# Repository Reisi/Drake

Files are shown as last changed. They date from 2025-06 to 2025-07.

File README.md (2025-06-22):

# Drake

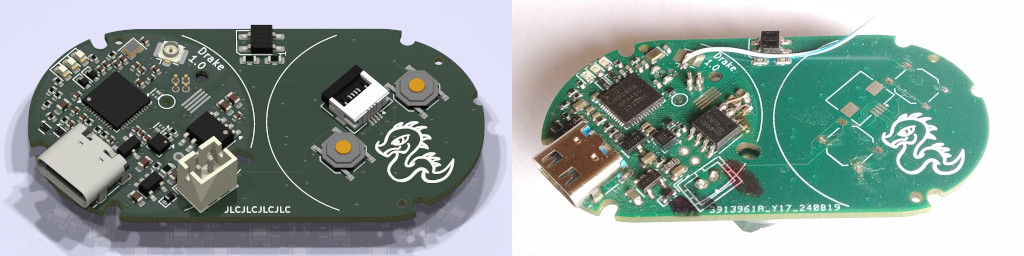
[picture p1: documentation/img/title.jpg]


The Drake hardware is a multi-purpose PCB which can be used to build a wireless dropper post actuator or a rear light.

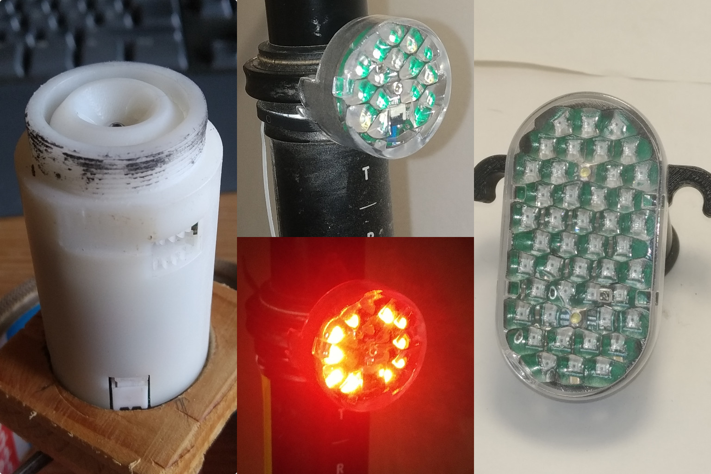
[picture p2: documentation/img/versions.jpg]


## Actuator

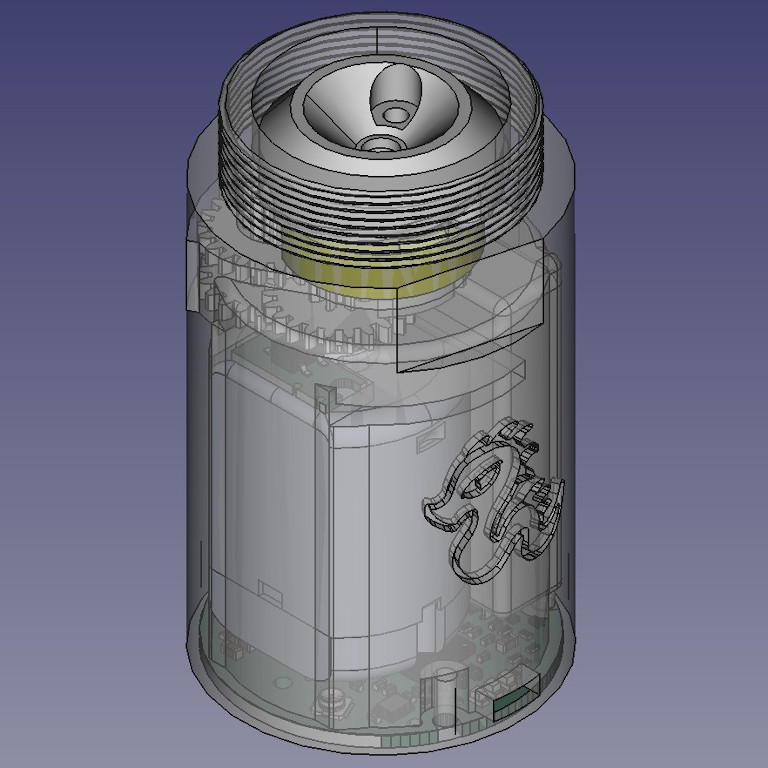
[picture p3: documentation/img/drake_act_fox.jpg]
Actuator


### Features

- Bluetooth connectivity for remote control and configuration.
- I2C connectivity for control, configuration and sensor readings.
- construction files for Fox Transfer dropper posts available

## Light

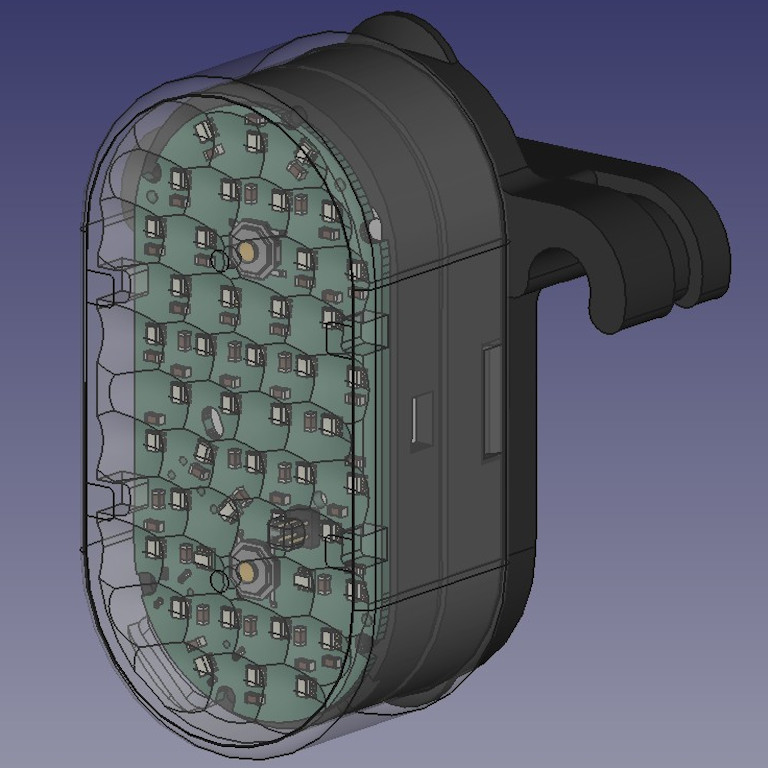
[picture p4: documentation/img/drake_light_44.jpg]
Light_44
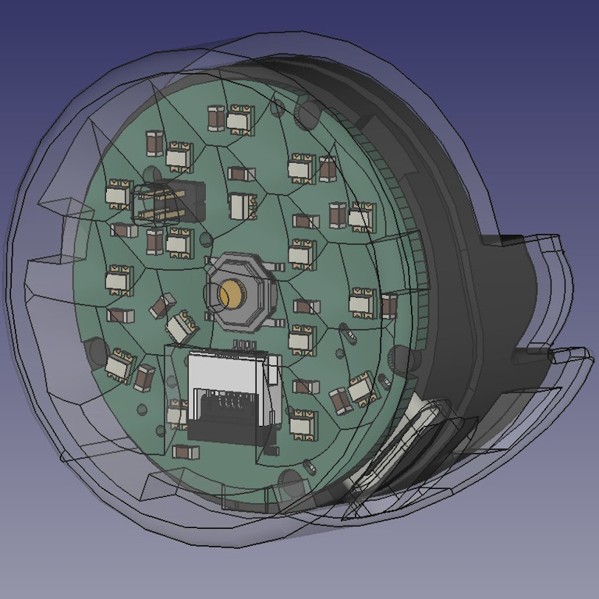
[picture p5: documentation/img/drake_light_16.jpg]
Light_16
 

### Features

- two configurations with either 16 or 44 WS2812 LEDs
- 8 configurable modes
- configurable LED pattern
- ability to control a dropper actuator over a FFC (using I2C)

## Firmware

Drake is part of The Helen Project. The source code and compiled firmware files are available [here](https://github.com/Reisi/The_Helen_Project/tree/master/Firmware/Helen/boards/Drake_10)

## License

This project is licensed under the BSD-2-clause License - see the [license.txt](license.txt) file for details

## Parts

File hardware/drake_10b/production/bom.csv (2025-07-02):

Designator | Footprint | Quantity | Value | LCSC Part #
AE2 | U.FL_Hirose_U.FL-R-SMT-1_Vertical | 1 | GT-RF1125A-01G | C5299419
C1, C2, C69, C70 | 0402 | 4 | 12p | C1547
C10, C12, C13, C15, C18 | 0603 | 5 | 10u | C19702
C14, C16, C20, C4, C66, C68, C8, C9 | 0402 | 8 | 100n | C307331
C17, C19, C7 | 0402 | 3 | 1u | C52923
C21, C22, C23, C24, C25, C26, C27, C28, C29, C30, C31, C32, C33, C34, C35, C36, C37, C38, C39, C40, C41, C42, C43, C44, C45, C46, C47, C48, C49, C50, C51, C52, C53, C54, C55, C56, C57, C58, C59, C60, C61, C62, C63, C64, C65, C67 | 0603 | 46 | 100n | C14663
C3 | 0402 | 1 | 0p8 | C1550
C6 | 0402 | 1 | 100p | C1546
D1, D15, D2 | D_SOD-523 | 3 | H5VND5UB | C20615819
D10, D11, D12, D13, D14, D17, D18, D19, D20, D22, D23, D24, D25, D26, D27, D28, D29, D30, D31, D32, D33, D34, D35, D36, D37, D38, D39, D40, D41, D42, D43, D44, D45, D46, D47, D48, D49, D50, D51, D52, D53, D55, D7, D8, D9 | LED_WS2812B-2020_PLCC4_2.0x2.0mm | 45 | WS2812B-2020 | C2976072
D16, D21, D3, D54 | Diodes_DFN1006-3 | 4 | H5VU13U | C20615795
D4 | 0603 | 1 | red | C2286
D5 | 0603 | 1 | yellow | C89811
D6 | 0603 | 1 | white | C2290
J2 | USB_C_Receptacle_XKB_U262-16XN-4BVC11 | 1 | USB_C_Receptacle_USB2.0_16P | C2931474
J3 | JST_PH_B2B-PH-K_1x02_P2.00mm_Vertical | 1 | Li-Ion | C131337
J5, J6, J8 | Jushuo_AFC01-S04FCC-00_1x04-1MP_P0.50_Horizontal | 3 | Conn_01x04 | C262260
JP1 | 0402 | 1 | Jumper_2_Bridged | C17168
L1 | 0402 | 1 | 3n9 | C14033
R1, R2 | 0402 | 2 | 22 | C25092
R10, R3, R8 | 0402 | 3 | 1M | C26083
R11, R12, R15, R16, R4 | 0402 | 5 | 3k3 | C25890
R13 | 0402 | 1 | 75k | C25798
R14, R17, R18 | 0402 | 3 | 1k5 | C25867
R5, R7, R9 | 0402 | 3 | 5k1 | C25905
R6 | 0603 | 1 | 2r2 | C22939
SW1, SW2, SW3, SW4 | SW_Push_1P1T_XKB_TS-1187A | 4 | SW_Push | C318884
U1 | QFN-48-1EP_6x6mm_P0.4mm_EP4.6x4.6mm | 1 | nRF52832-QFxx | C77540
U2 | SOT-23-3 | 1 | XC6206P332MR-G | C5446
U3 | SOT-23-5 | 1 | TP4054 | C32574
U4 | LGA-12_2x2mm_P0.5mm | 1 | LIS2DH12TR | C110926
U5 | SOIC-8_3.9x4.9mm_P1.27mm | 1 | BDR6125
U6 | Everlight_ITR1201SR10AR | 1 | ITR8307-S18-TR8 | C409524
Y1 | Crystal_SMD_2016-4Pin_2.0x1.6mm | 1 | Crystal_GND24 | C2965584

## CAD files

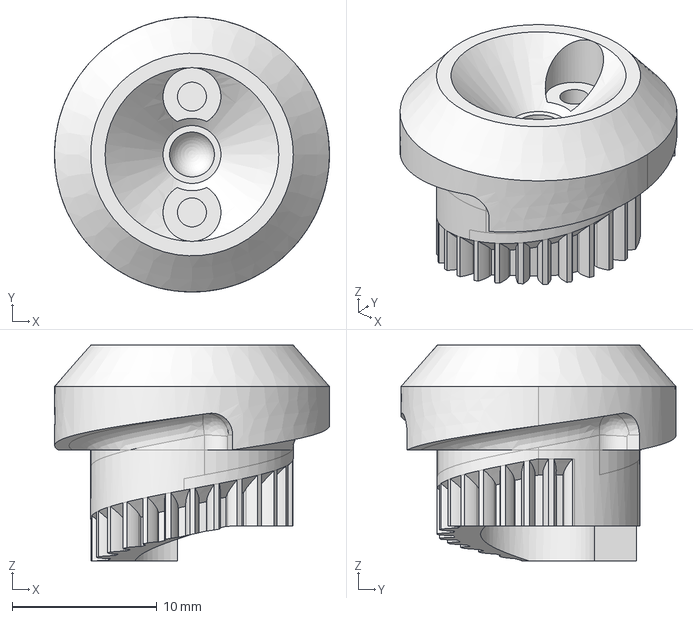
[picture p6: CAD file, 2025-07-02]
construction/Drake_Fox/Drake_Fox_2208_v2b-plunger.step
19.0 x 19.0 x 14.9 mm

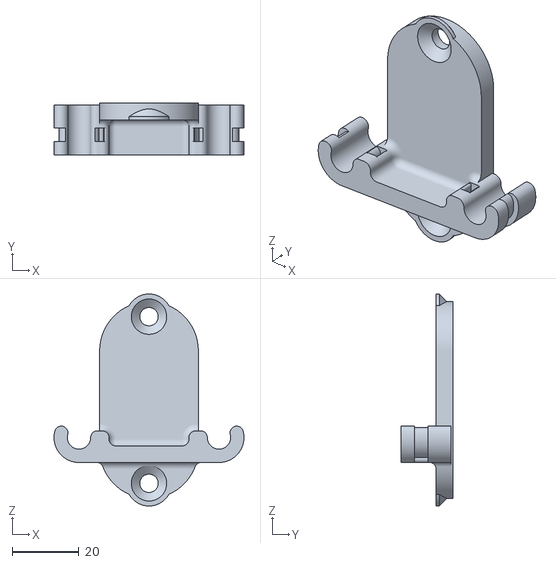
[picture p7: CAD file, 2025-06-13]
construction/Drakelight/Drakelight_MountVertical.stl
57.0 x 15.5 x 63.6

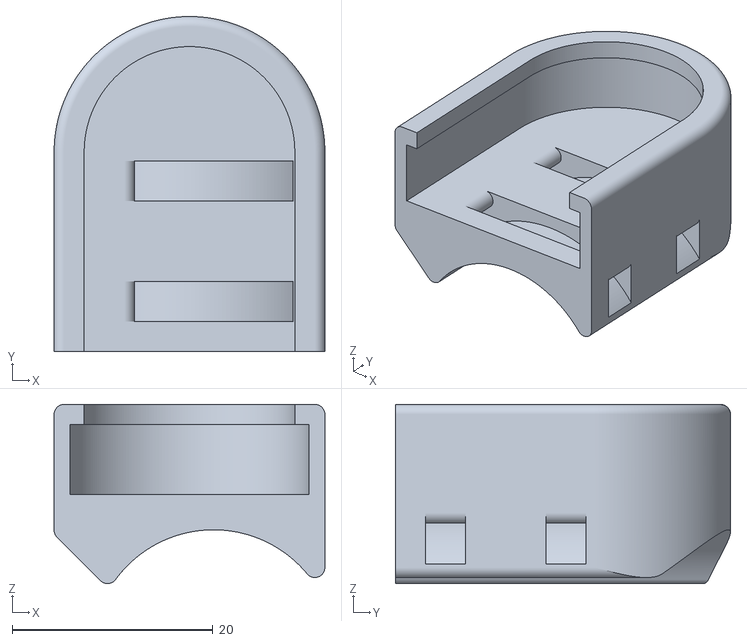
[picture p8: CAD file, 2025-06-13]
construction/Remote_Mount/XiaomiYiMount_hor.stl
27.0 x 33.4 x 17.9

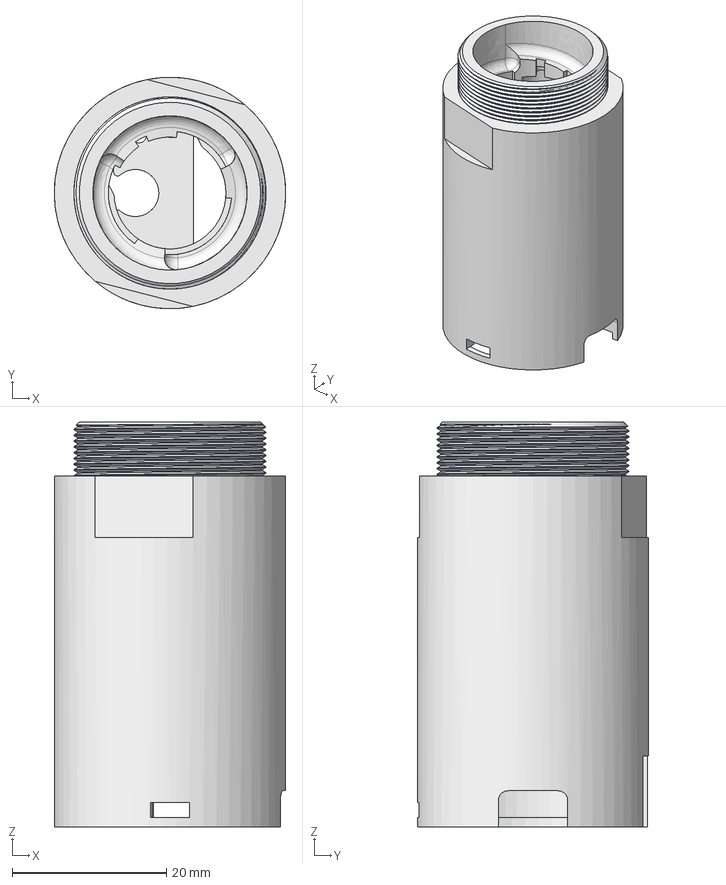
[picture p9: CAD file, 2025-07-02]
construction/Drake_Fox/Drake_Fox_2208_v2b-case.step
30.0 x 30.0 x 52.5 mm

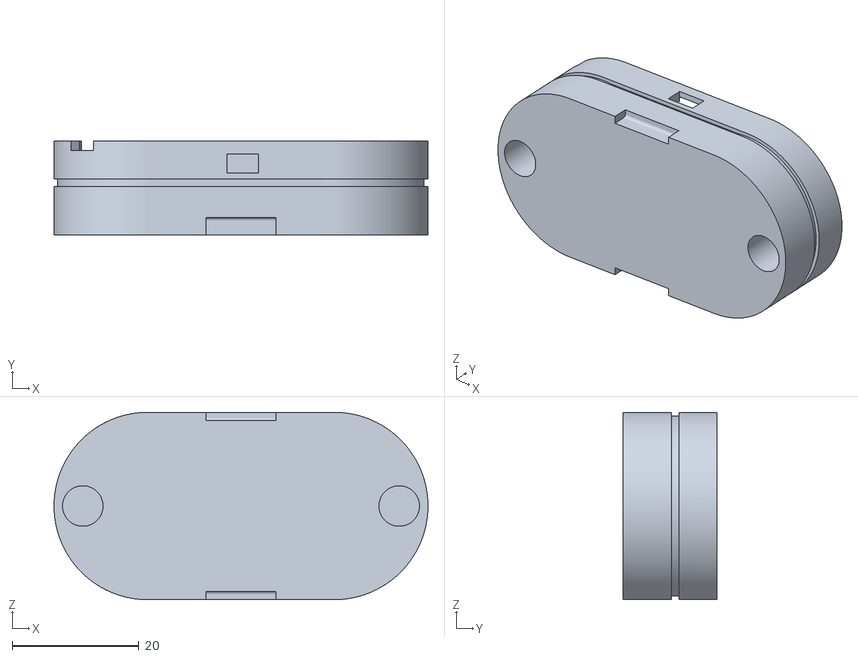
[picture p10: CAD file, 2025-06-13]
construction/Drakelight/Drakelight_case.stl
59.1 x 14.8 x 29.6

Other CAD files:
construction/Remote_Mount/XiaomiYiMount.FCStd
construction/Drake_Fox/Drake_Fox_2208_v2b-plunger.stl

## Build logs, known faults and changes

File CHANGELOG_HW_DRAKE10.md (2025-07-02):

# Changelog
All notable changes to the Drake board hardware will be documented in this file.

The format is based on [Keep a Changelog](https://keepachangelog.com/en/1.0.0/)

## [1.1] - 2025-07
### Added

### Changed
- changed acceleration sensor to MMA8451Q
- changed motor driver to DRV8213

### Removed

### Fixed

### Known Issues

## [1.0b] - 2025-06
### Changed
- changed green LED to yellow and blue LED to white

### Fixed
- fixed swapped power supply pins for motor driver
- changed R13 value to 82k

## [1.0] - 2024-08
### Known Issues
- VCC and GND pin swapped on moter driver
- R13 changed from 1k5 to 82k (ir receiver resitor)

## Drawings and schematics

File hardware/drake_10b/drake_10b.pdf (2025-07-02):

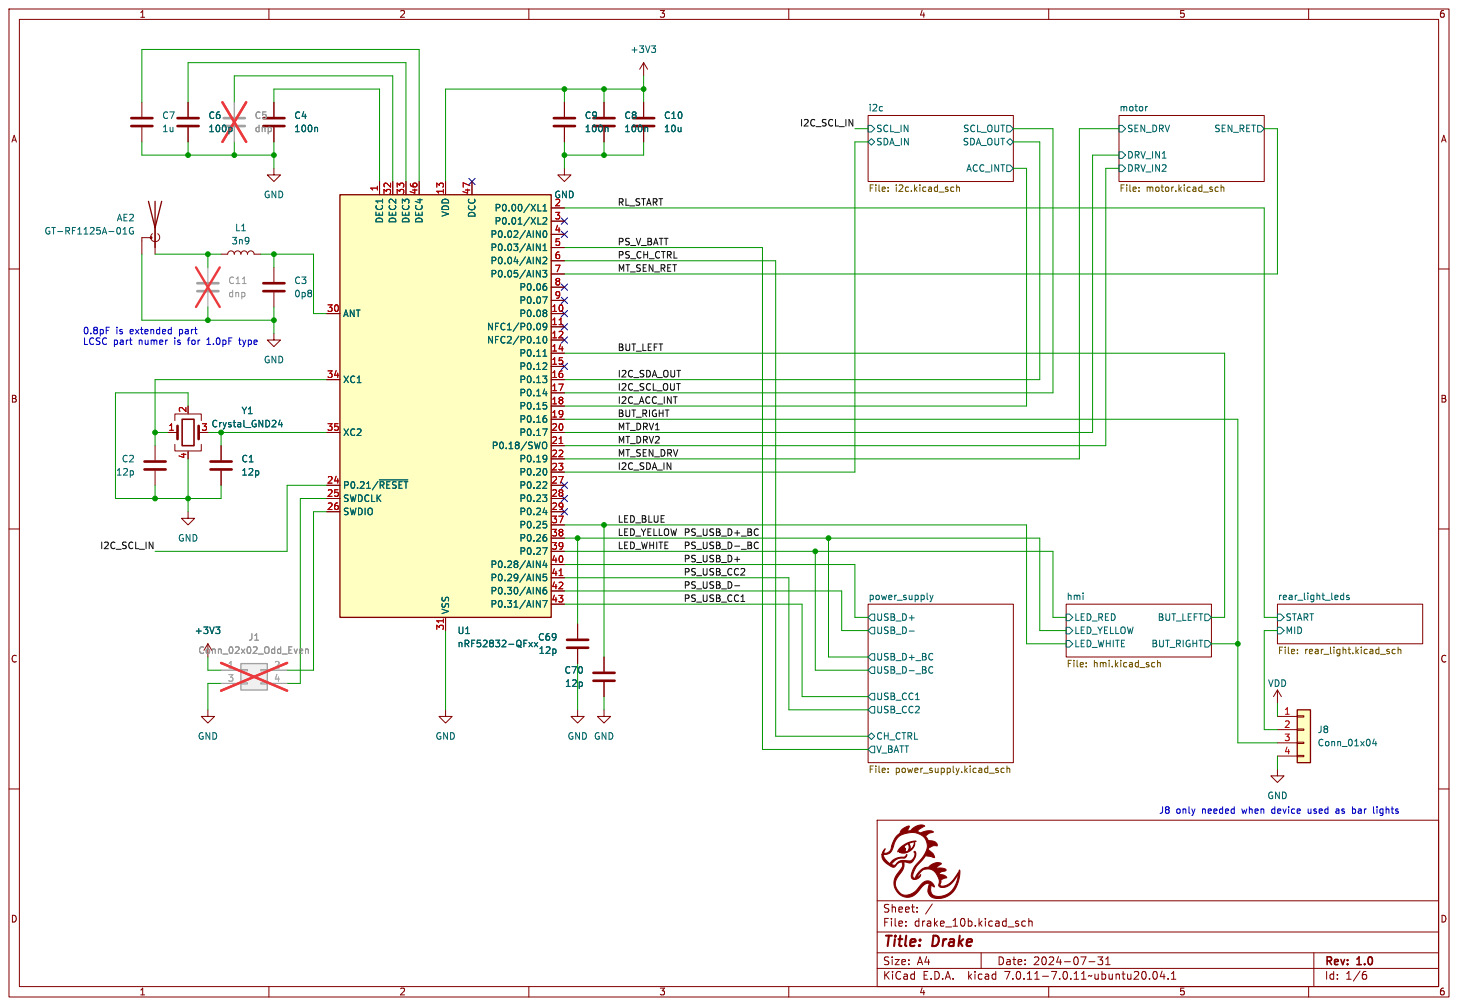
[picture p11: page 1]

1 P0.08 10 NFC1/P0.09 11 NFC2/P0.10 12 VDD 13 P0.11 14 P0.12 15 P0.13 16 P0.14 17 P0.15 18 P0.16 19 P0.00/XL1 2 P0.17 20 P0.18/SWO 21 P0.19 22 P0.20 23 P0.21/~{RESET} 24 SWDCLK 25 SWDIO 26 P0.22 27 P0.23 28 P0.24 29 P0.01/XL2 3 ANT 30 VSS 31 DEC2 32 DEC3 33 XC1 34 XC2 35 P0.25 37 P0.26 38 P0.27 39 P0.02/AIN0 4 P0.28/AIN4 40 P0.29/AIN5 41 P0.30/AIN6 42 P0.31/AIN7 43 DEC4 46 DCC 47 P0.03/AIN1 5 P0.04/AIN2 6 P0.05/AIN3 7 P0.06 8 P0.07 9 U1

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

J8 only needed when device used as bar lights

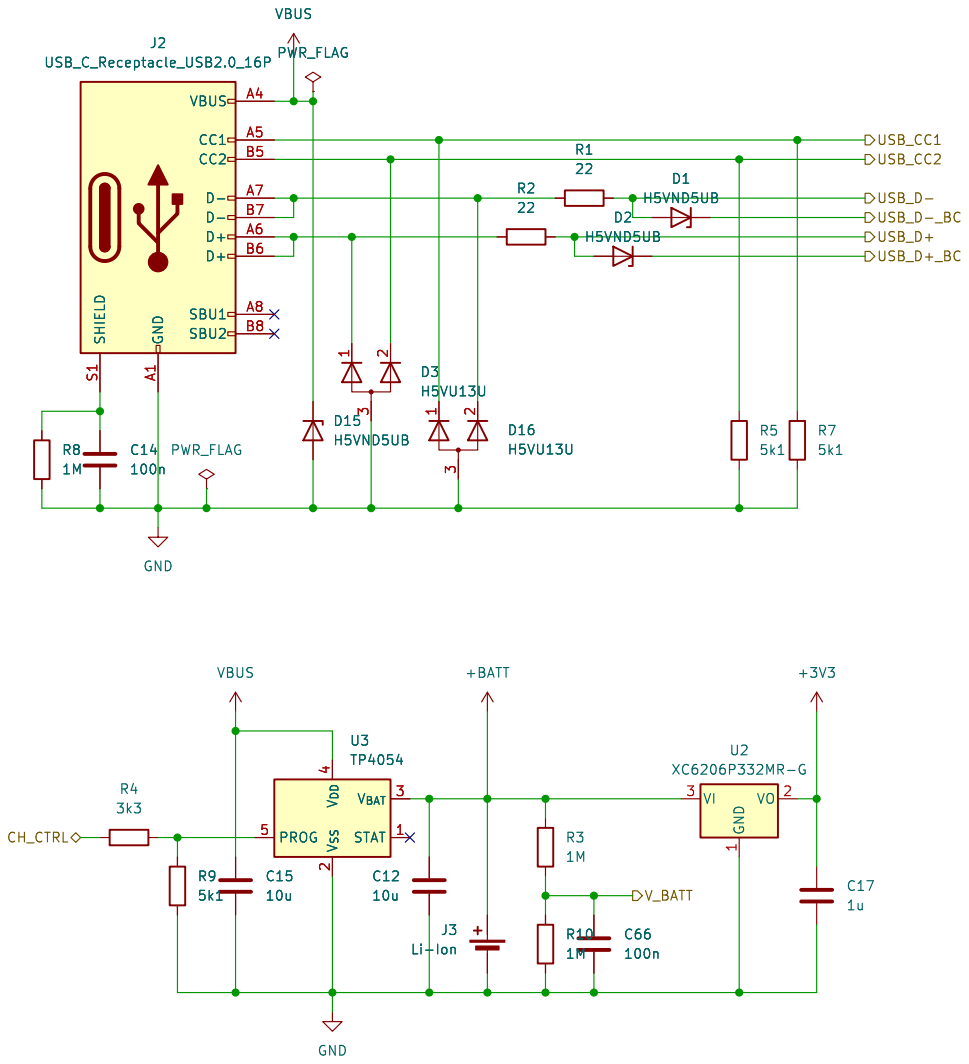
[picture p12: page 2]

File: power_supply.kicad_sch Sheet: /power_supply/
Id: 2/6 Title: power supply

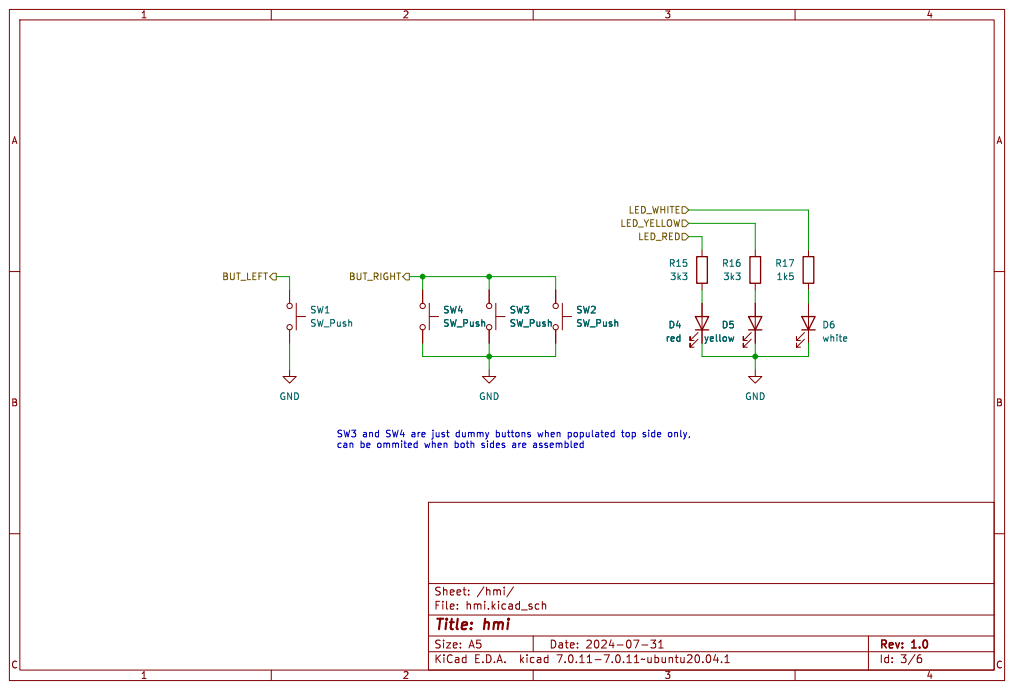
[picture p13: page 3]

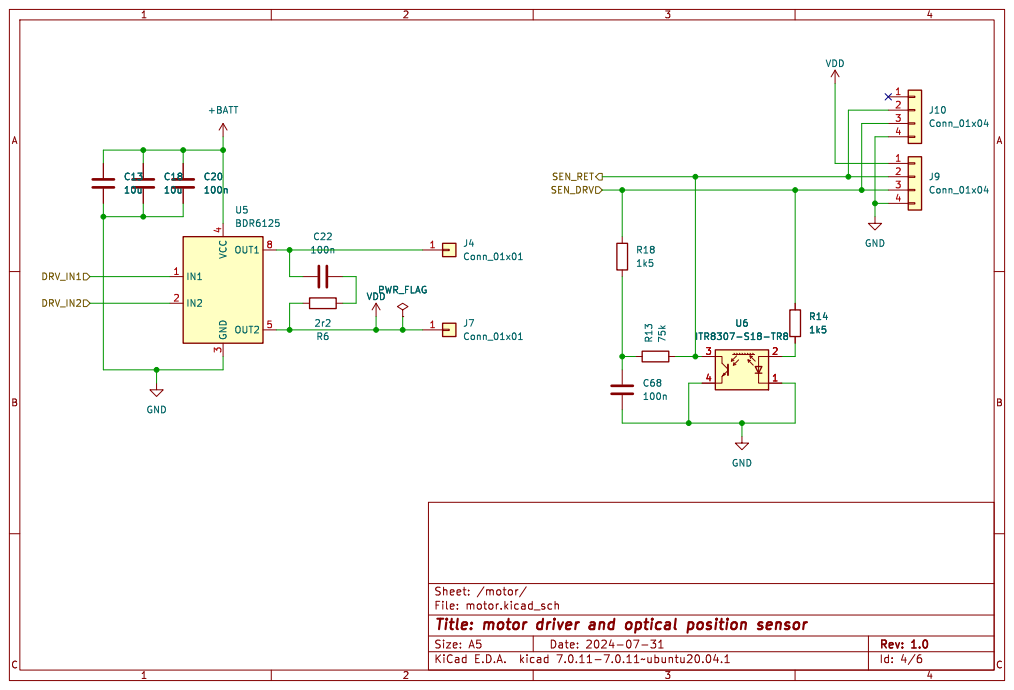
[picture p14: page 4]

Id: 4/6 Title: motor driver and optical position sensor File: motor.kicad_sch Sheet: /motor/ R6

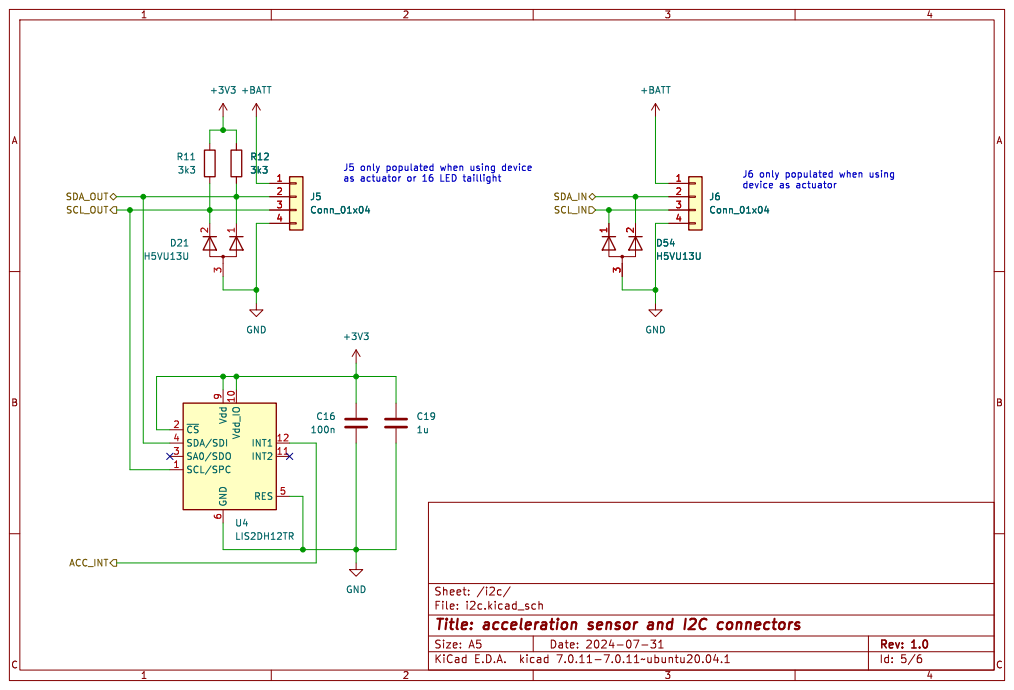
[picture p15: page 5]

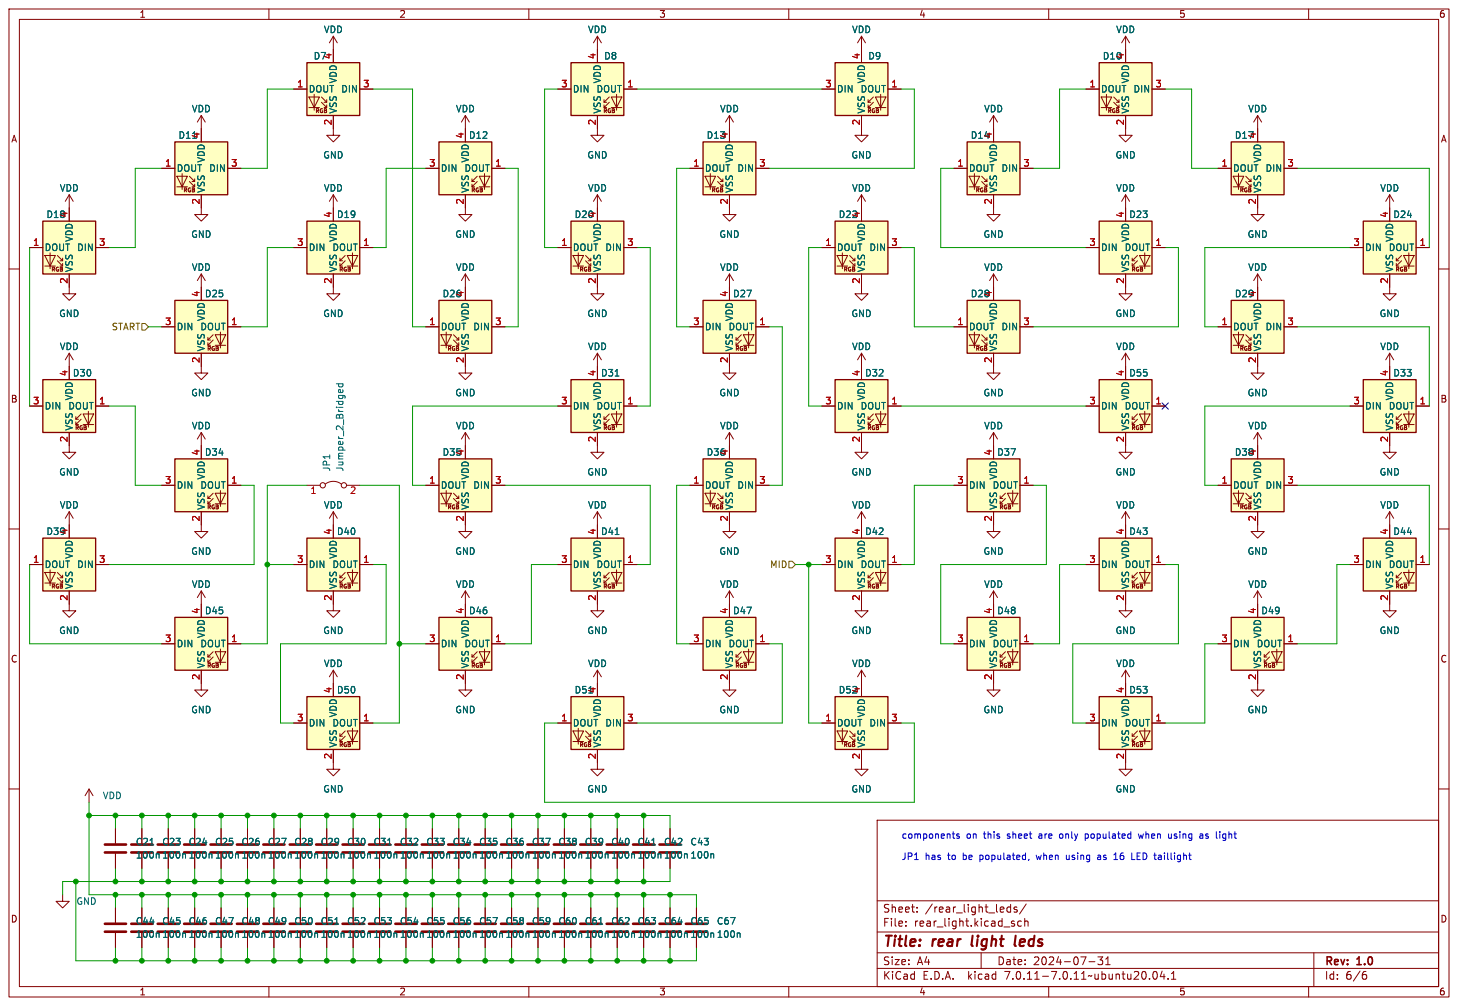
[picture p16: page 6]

4D53 VDD GND GND GND

Id: 6/6 Title: rear light leds

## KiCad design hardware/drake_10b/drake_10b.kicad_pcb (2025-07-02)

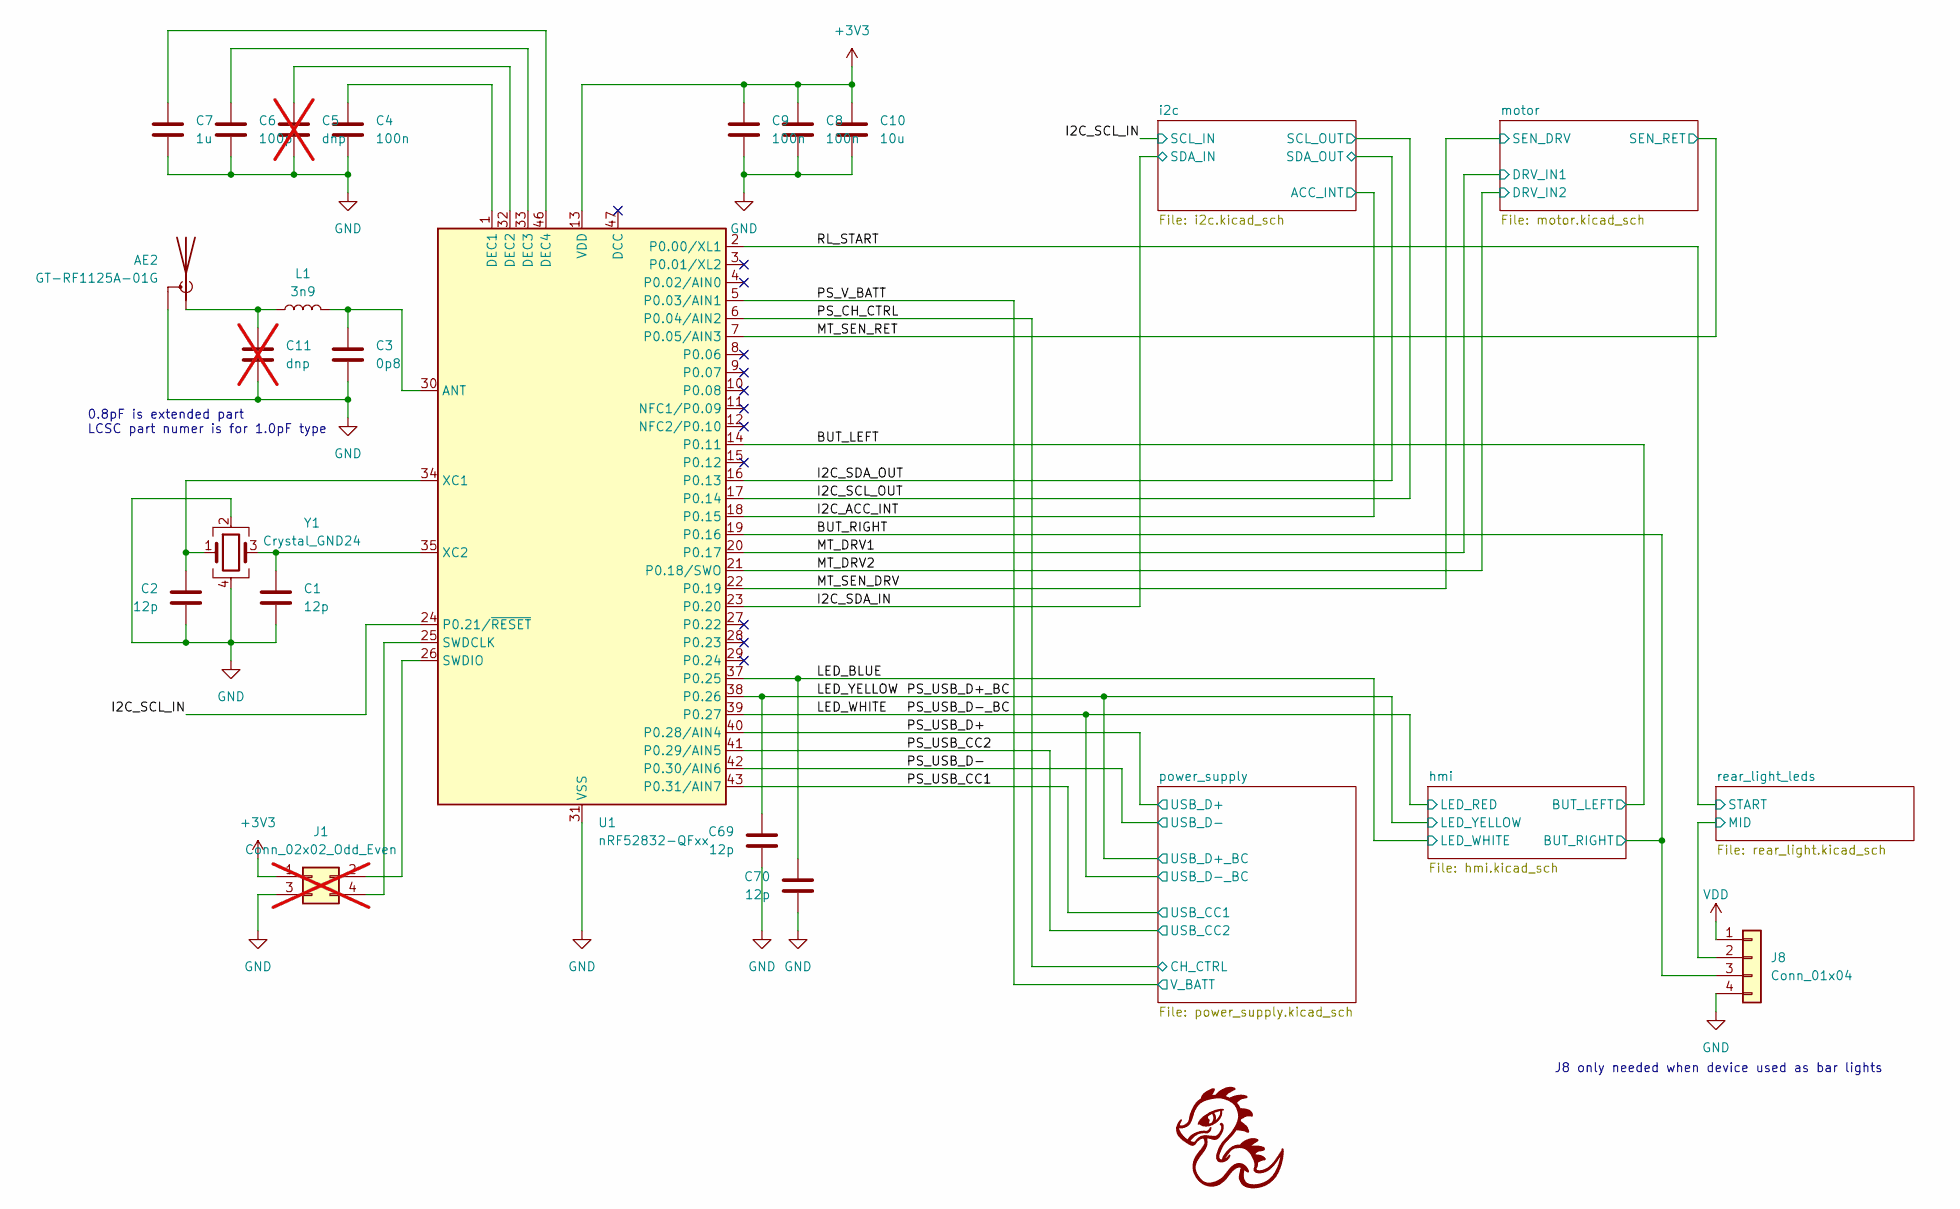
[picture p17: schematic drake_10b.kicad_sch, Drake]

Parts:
AE2: GT-RF1125A-01G; U.FL_Hirose_U.FL-R-SMT-1_Vertical; JLC SMD
C1, C2, C69, C70: 12p; C_0402_1005Metric; JLC 0402
C3: 0p8; C_0402_1005Metric; JLC 0402
C4, C8, C9: 100n; C_0402_1005Metric; JLC 0402
C5, C11: dnp; C_0402_1005Metric; not fitted
C6: 100p; C_0402_1005Metric; JLC 0402
C7: 1u; C_0402_1005Metric; JLC 0402
C10: 10u; C_0603_1608Metric; JLC 0603
J1: Conn_02x02_Odd_Even; PinHeader_2x02_P1.27mm_Vertical; not fitted
J8: Conn_01x04; Jushuo_AFC01-S04FCC-00_1x04-1MP_P0.50_Horizontal; JLC SMD,P=0.5mm
L1: 3n9; L_0402_1005Metric; JLC 0402
U1: nRF52832-QFxx; QFN-48-1EP_6x6mm_P0.4mm_EP4.6x4.6mm; JLC QFN-48-EP(6x6)
Y1: Crystal_GND24; Crystal_SMD_2016-4Pin_2.0x1.6mm; JLC SMD2016-4P

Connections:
+3V3: C8.1, C9.1, C10.1, J1.1, U1.13 (VDD), U1.36 (VDD), U1.48 (VDD); also elsewhere on the board
/BUT_LEFT: U1.14 (P0.11); also elsewhere on the board
/BUT_RIGHT: J8.3, U1.19 (P0.16); also elsewhere on the board
/I2C_ACC_INT: U1.18 (P0.15); also elsewhere on the board
/I2C_SCL_IN: U1.24 (P0.21/~RESET); also elsewhere on the board
/I2C_SCL_OUT: U1.17 (P0.14); also elsewhere on the board
/I2C_SDA_IN: U1.23 (P0.20); also elsewhere on the board
/I2C_SDA_OUT: U1.16 (P0.13); also elsewhere on the board
/LED_BLUE: C70.1, U1.37 (P0.25); also elsewhere on the board
/LED_WHITE: U1.39 (P0.27); also elsewhere on the board
/LED_YELLOW: C69.1, U1.38 (P0.26); also elsewhere on the board
/MT_DRV1: U1.20 (P0.17); also elsewhere on the board
/MT_DRV2: U1.21 (P0.18/SWO); also elsewhere on the board
/MT_SEN_DRV: U1.22 (P0.19); also elsewhere on the board
/MT_SEN_RET: U1.7 (P0.05/AIN3); also elsewhere on the board
/PS_CH_CTRL: U1.6 (P0.04/AIN2); also elsewhere on the board
/PS_USB_CC1: U1.43 (P0.31/AIN7); also elsewhere on the board
/PS_USB_CC2: U1.41 (P0.29/AIN5); also elsewhere on the board
/PS_USB_D+: U1.40 (P0.28/AIN4); also elsewhere on the board
/PS_USB_D-: U1.42 (P0.30/AIN6); also elsewhere on the board
/PS_V_BATT: U1.5 (P0.03/AIN1); also elsewhere on the board
/RL_START: U1.2 (P0.00/XL1); also elsewhere on the board
/rear_light_leds/MID: J8.2; also elsewhere on the board
GND: AE2.2 (Shield), C1.2, C2.2, C3.2, C4.2, C5.2, C6.2, C7.2, C8.2, C9.2, C10.2, C11.2, C69.2, C70.2, J1.3, J8.4, U1.31 (VSS), U1.45 (VSS), U1.49 (VSS), Y1.2, Y1.4; also elsewhere on the board
unnamed: AE2.1 (A), C11.1, L1.1
unnamed: J1.2, U1.26 (SWDIO)
unnamed: J1.4, U1.25 (SWDCLK)
unnamed: C3.1, L1.2, U1.30 (ANT)
unnamed: C4.1, U1.1 (DEC1)
unnamed: C5.1, U1.32 (DEC2)
unnamed: C6.1, U1.33 (DEC3)
unnamed: C7.1, U1.46 (DEC4)
unnamed: C2.1, U1.34 (XC1), Y1.1
unnamed: C1.1, U1.35 (XC2), Y1.3
VDD: J8.1; also elsewhere on the board

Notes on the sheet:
J8 only needed when device used as bar lights
0.8pF is extended part LCSC part numer is for 1.0pF type

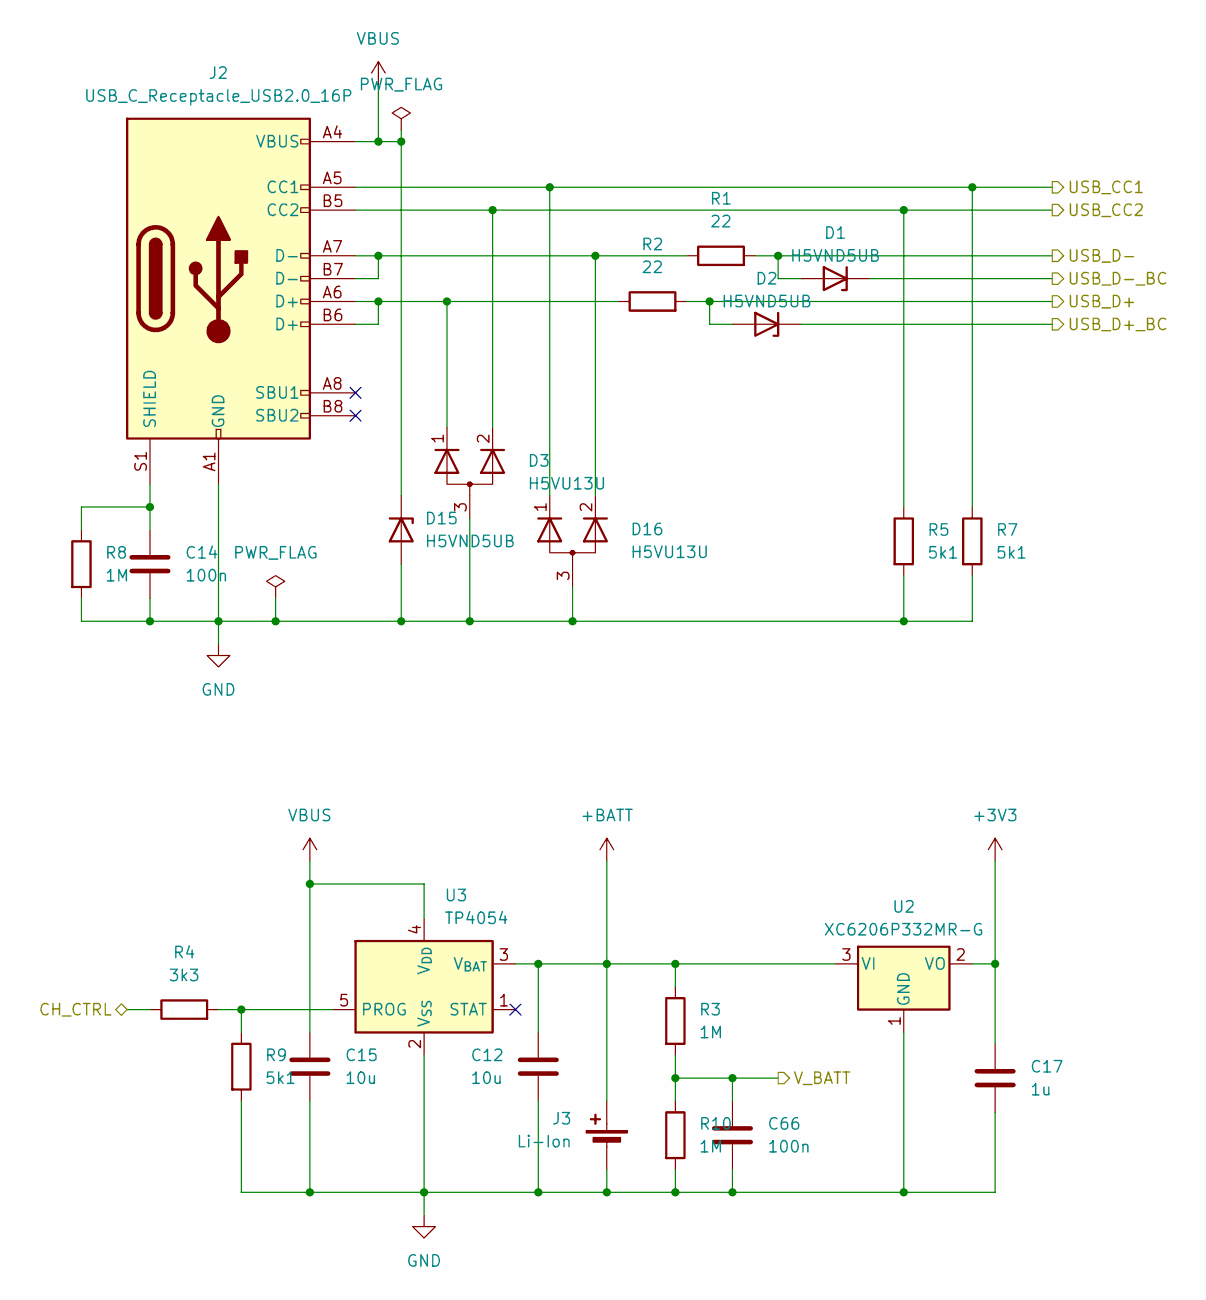
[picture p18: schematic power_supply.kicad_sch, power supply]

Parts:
C12, C15: 10u; C_0603_1608Metric; JLC 0603
C14, C66: 100n; C_0402_1005Metric; JLC 0402
C17: 1u; C_0402_1005Metric; JLC 0402
D1, D2, D15: H5VND5UB; D_SOD-523; JLC SOD-523
D3, D16: H5VU13U; Diodes_DFN1006-3; JLC DFN1006-3L
J2: USB_C_Receptacle_USB2.0_16P; USB_C_Receptacle_XKB_U262-16XN-4BVC11; JLC SMD
J3: Li-Ion; JST_PH_B2B-PH-K_1x02_P2.00mm_Vertical; JLC Plugin,P=2mm
R1, R2: 22; R_0402_1005Metric; JLC 0402
R3, R8, R10: 1M; R_0402_1005Metric; JLC 0402
R4: 3k3; R_0402_1005Metric; JLC 0402
R5, R7, R9: 5k1; R_0402_1005Metric; JLC 0402
U2: XC6206P332MR-G; SOT-23-3; JLC SOT-23-3L
U3: TP4054; SOT-23-5; LCSC C32574

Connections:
+3V3: C17.1, U2.2 (VO); also elsewhere on the board
+BATT: C12.1, J3.2 (+), R3.1, U2.3 (VI), U3.3 (V_{BAT}); also elsewhere on the board
/LED_WHITE: D1.1 (K); also elsewhere on the board
/LED_YELLOW: D2.1 (K); also elsewhere on the board
/PS_CH_CTRL: R4.1; also elsewhere on the board
/PS_USB_CC1: D16.1 (K), J2.A5 (CC1), R7.1; also elsewhere on the board
/PS_USB_CC2: D3.2 (K), J2.B5 (CC2), R5.1; also elsewhere on the board
/PS_USB_D+: D2.2 (A), R2.2; also elsewhere on the board
/PS_USB_D-: D1.2 (A), R1.2; also elsewhere on the board
/PS_V_BATT: C66.1, R3.2, R10.1; also elsewhere on the board
GND: C12.2, C14.2, C15.2, C17.2, C66.2, D3.3 (A), D15.2 (A), D16.3 (A), J2.A1 (GND), J2.A12 (GND), J2.B1 (GND), J2.B12 (GND), J3.1 (-), R5.2, R7.2, R8.2, R9.2, R10.2, U2.1 (GND), U3.2 (V_{SS}); also elsewhere on the board
unnamed: D3.1 (K), J2.A6 (D+), J2.B6 (D+), R2.1
unnamed: D16.2 (K), J2.A7 (D-), J2.B7 (D-), R1.1
unnamed: C14.1, J2.S1 (SHIELD), R8.1
unnamed: R4.2, R9.1, U3.5 (PROG)
VBUS: C15.1, D15.1 (K), J2.A4 (VBUS), J2.A9 (VBUS), J2.B4 (VBUS), J2.B9 (VBUS), U3.4 (V_{DD})

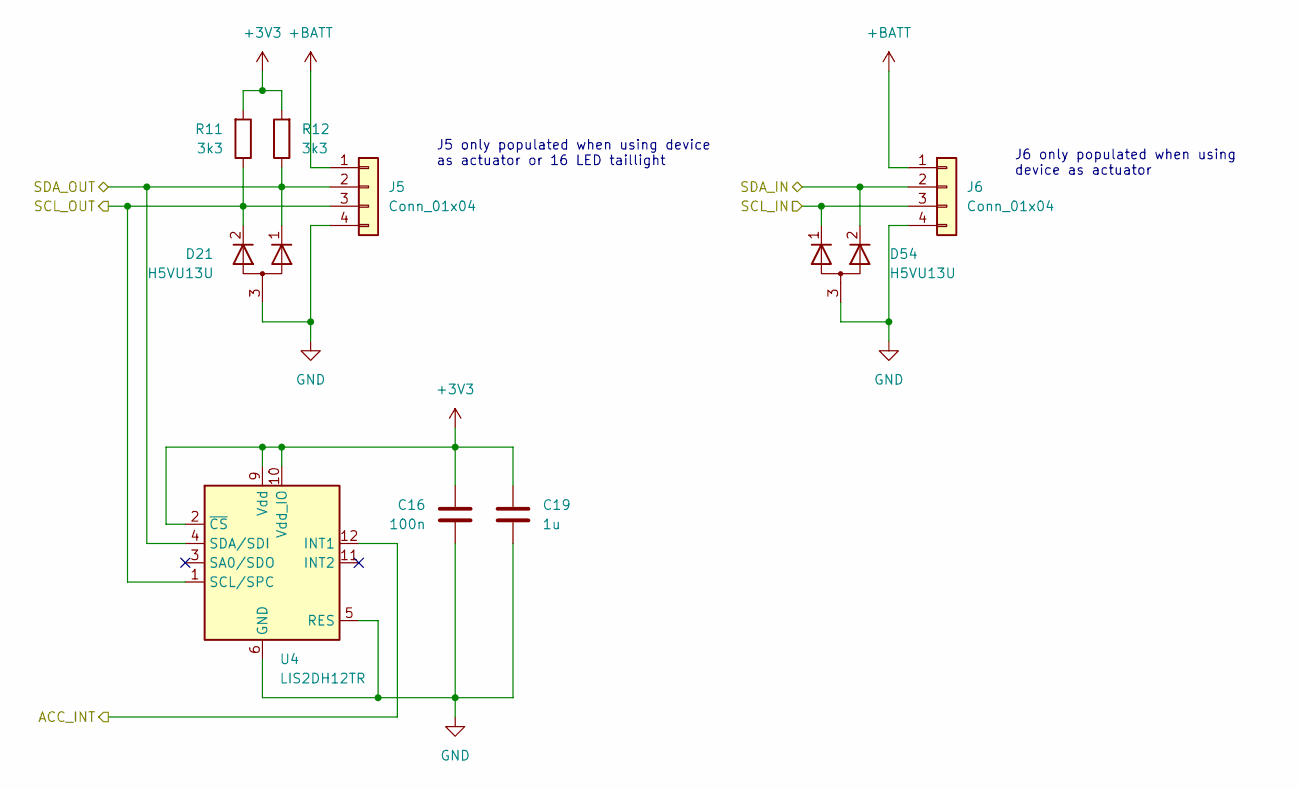
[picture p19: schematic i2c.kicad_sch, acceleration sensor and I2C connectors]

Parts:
C16: 100n; C_0402_1005Metric; JLC 0402
C19: 1u; C_0402_1005Metric; JLC 0402
D21, D54: H5VU13U; Diodes_DFN1006-3; JLC DFN1006-3L
J5, J6: Conn_01x04; Jushuo_AFC01-S04FCC-00_1x04-1MP_P0.50_Horizontal; JLC SMD,P=0.5mm
R11, R12: 3k3; R_0402_1005Metric; JLC 0402
U4: LIS2DH12TR; LGA-12_2x2mm_P0.5mm; JLC LGA-12

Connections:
+3V3: C16.1, C19.1, R11.2, R12.2, U4.2 (~CS), U4.9 (Vdd), U4.10 (Vdd_IO); also elsewhere on the board
+BATT: J5.1, J6.1; also elsewhere on the board
/I2C_ACC_INT: U4.12 (INT1); also elsewhere on the board
/I2C_SCL_IN: D54.1 (K), J6.3; also elsewhere on the board
/I2C_SCL_OUT: D21.2 (K), J5.3, R11.1, U4.1 (SCL/SPC); also elsewhere on the board
/I2C_SDA_IN: D54.2 (K), J6.2; also elsewhere on the board
/I2C_SDA_OUT: D21.1 (K), J5.2, R12.1, U4.4 (SDA/SDI); also elsewhere on the board
GND: C16.2, C19.2, D21.3 (A), D54.3 (A), J5.4, J6.4, U4.5 (RES), U4.6 (GND), U4.7 (GND), U4.8 (GND); also elsewhere on the board

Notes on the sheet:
J6 only populated when using device as actuator
J5 only populated when using device as actuator or 16 LED taillight

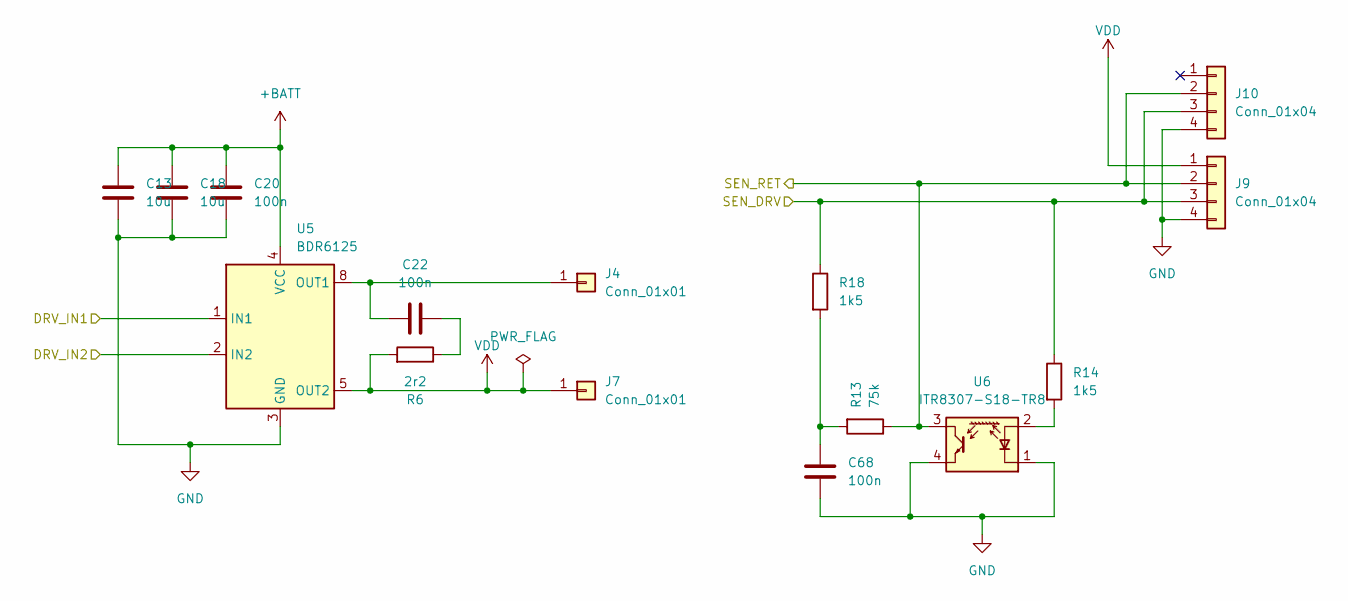
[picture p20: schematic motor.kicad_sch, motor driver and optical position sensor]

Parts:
C13, C18: 10u; C_0603_1608Metric; JLC 0603
C20, C68: 100n; C_0402_1005Metric; JLC 0402
C22: 100n; C_0603_1608Metric; JLC 0603
J4, J7: Conn_01x01; PinHeader_1x01_P2.00mm_Vertical
J9, J10: Conn_01x04; FFC_SolderCon_4pin_3,5x0,3mm_Pitch0.5mm; JLC SMD,P=0.5mm
R6: 2r2; R_0603_1608Metric; JLC 0603
R13: 75k; R_0402_1005Metric; JLC 0402
R14, R18: 1k5; R_0402_1005Metric; JLC 0402
U5: BDR6125; SOIC-8_3.9x4.9mm_P1.27mm
U6: ITR8307-S18-TR8; Everlight_ITR1201SR10AR; JLC SMD

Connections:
+BATT: C13.1, C18.1, C20.1, U5.4 (VCC); also elsewhere on the board
/MT_DRV1: U5.1 (IN1); also elsewhere on the board
/MT_DRV2: U5.2 (IN2); also elsewhere on the board
/MT_SEN_DRV: J9.3, J10.3, R14.1, R18.1; also elsewhere on the board
/MT_SEN_RET: J9.2, J10.2, R13.1, U6.3; also elsewhere on the board
GND: C13.2, C18.2, C20.2, C68.2, J9.4, J10.4, U5.3 (GND), U6.1 (K), U6.4; also elsewhere on the board
unnamed: C22.1, R6.1
unnamed: C68.1, R13.2, R18.2
unnamed: C22.2, J4.1, U5.7 (OUT1), U5.8 (OUT1)
unnamed: R14.2, U6.2 (A)
VDD: J7.1, J9.1, R6.2, U5.5 (OUT2), U5.6 (OUT2); also elsewhere on the board

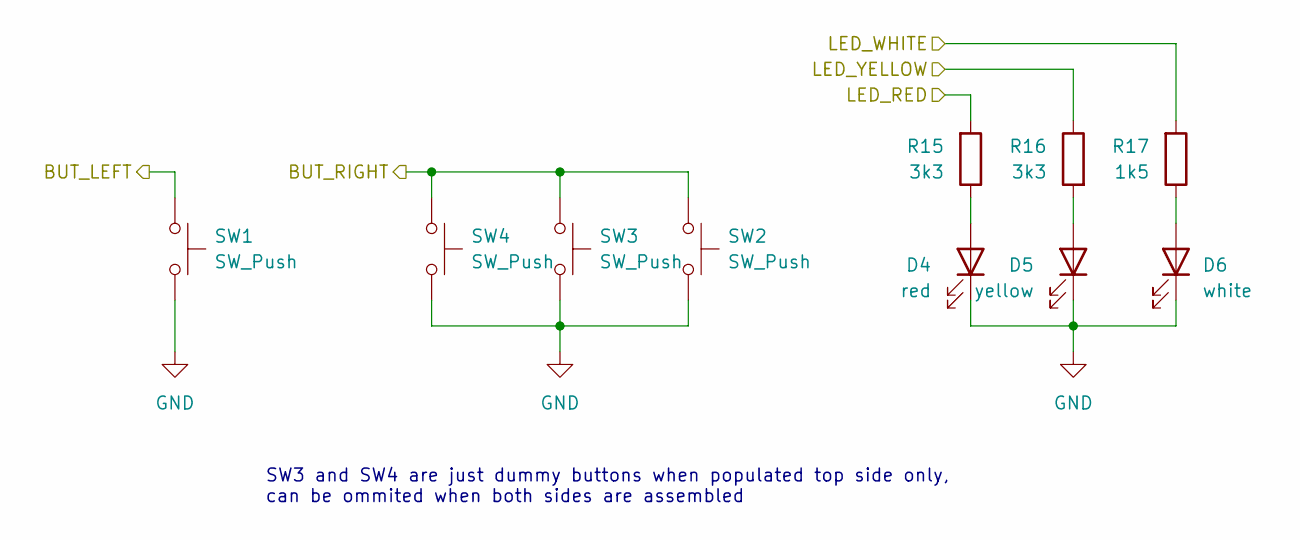
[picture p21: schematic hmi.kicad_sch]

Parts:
D4: red; LED_0603_1608Metric; JLC 0603
D5: yellow; LED_0603_1608Metric; JLC 0603
D6: white; LED_0603_1608Metric; LCSC C2290
R15, R16: 3k3; R_0402_1005Metric; JLC 0402
R17: 1k5; R_0402_1005Metric; JLC 0402
SW1, SW2, SW3, SW4: SW_Push; SW_Push_1P1T_XKB_TS-1187A; JLC SMD

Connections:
/BUT_LEFT: SW1.1; also elsewhere on the board
/BUT_RIGHT: SW2.1, SW3.1, SW4.1; also elsewhere on the board
/LED_BLUE: R17.2; also elsewhere on the board
/LED_WHITE: R15.2; also elsewhere on the board
/LED_YELLOW: R16.1; also elsewhere on the board
GND: D4.1 (K), D5.1 (K), D6.1 (K), SW1.2, SW2.2, SW3.2, SW4.2; also elsewhere on the board
unnamed: D4.2 (A), R15.1
unnamed: D5.2 (A), R16.2
unnamed: D6.2 (A), R17.1

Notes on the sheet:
SW3 and SW4 are just dummy buttons when populated top side only, can be ommited when both sides are assembled

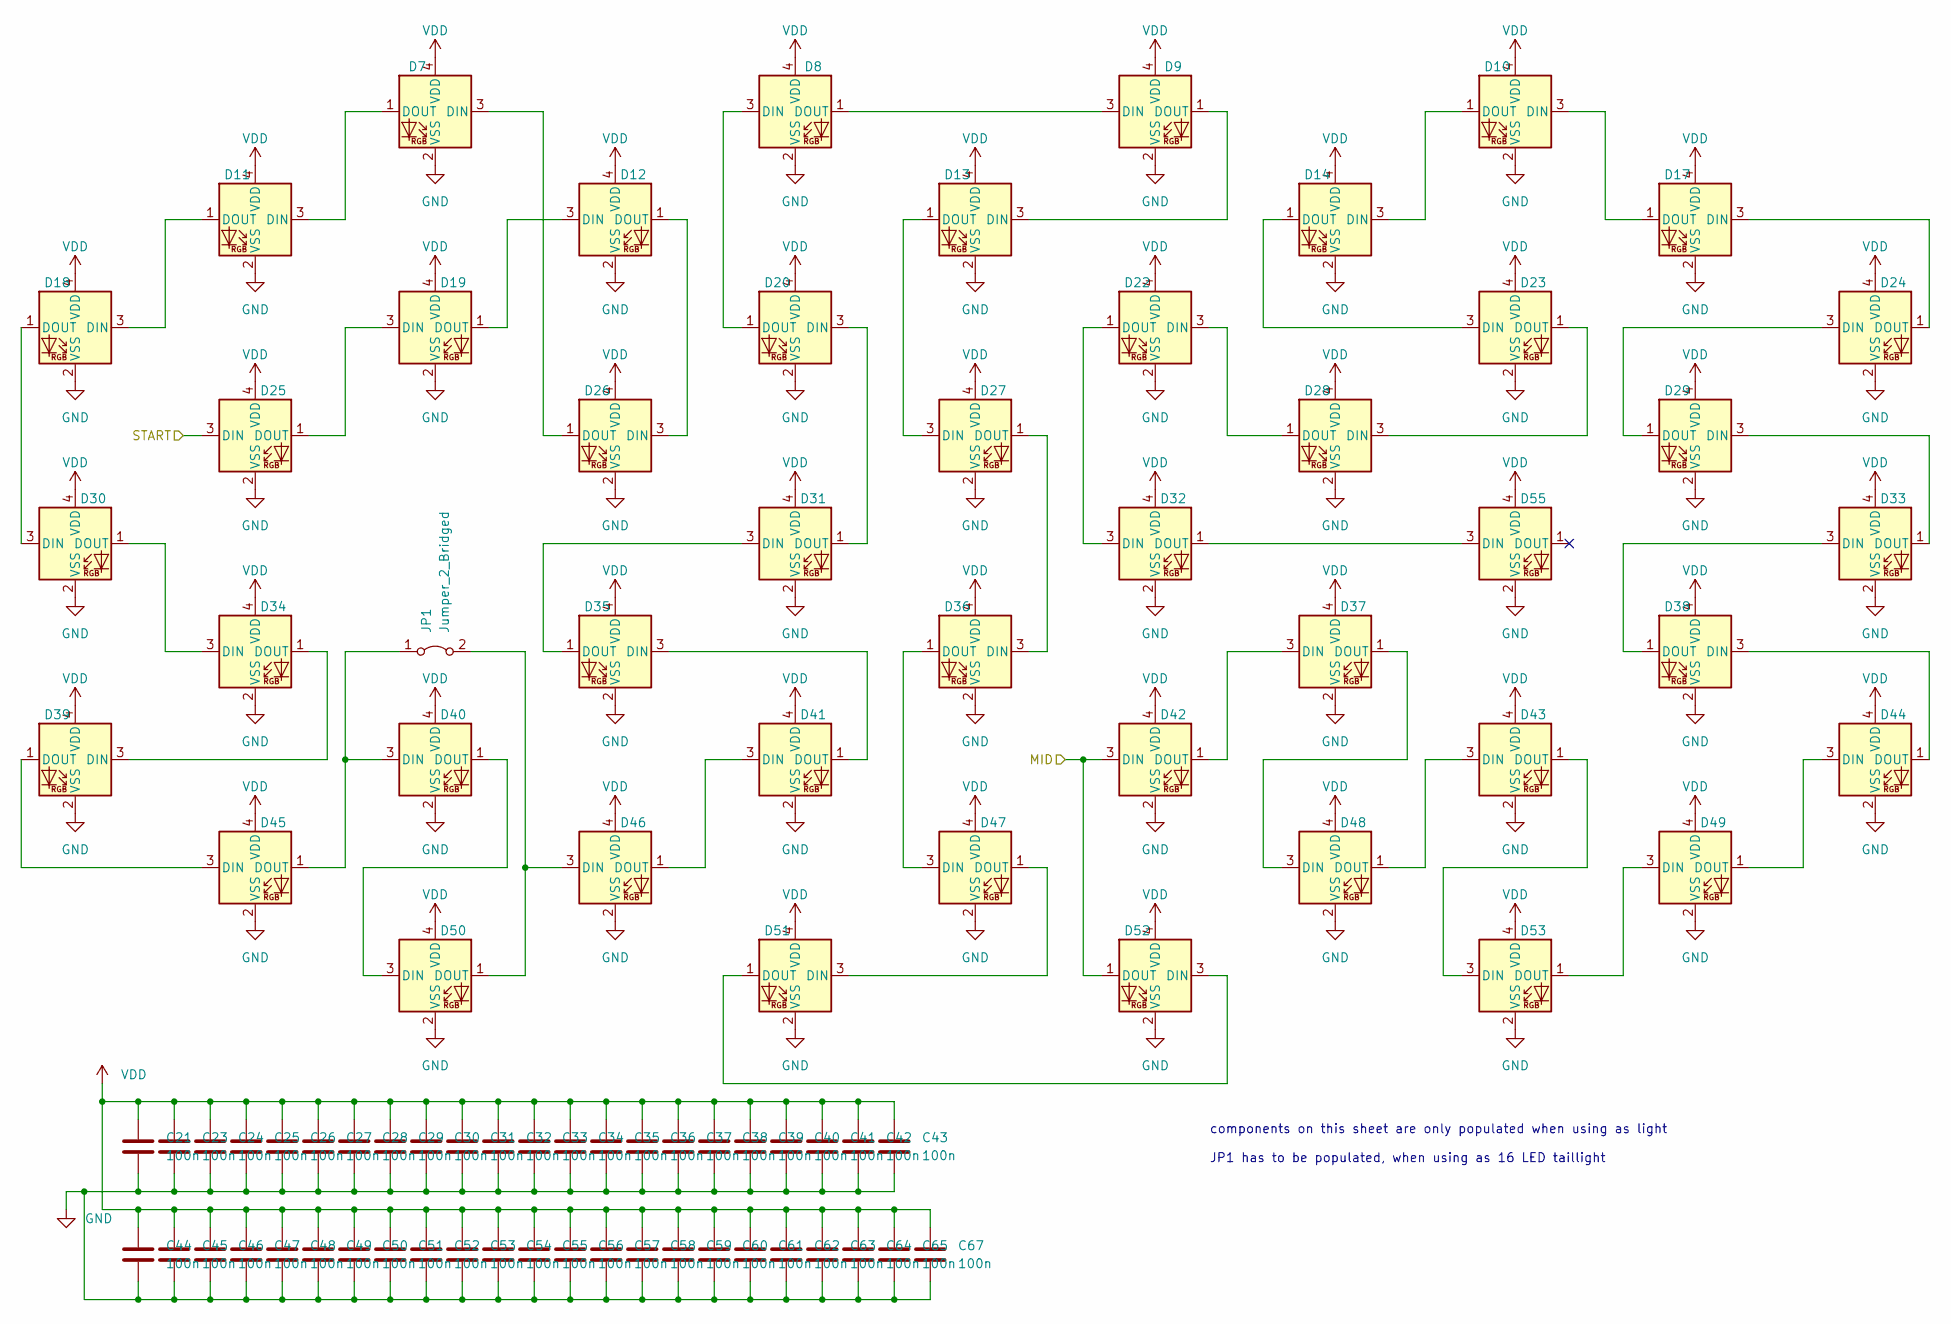
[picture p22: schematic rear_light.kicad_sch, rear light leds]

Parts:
C21, C23, C24, C25, C26, C27, C28, C29, C30, C31, C32, C33, C34, C35, C36, C37, C38, C39, C40, C41, C42, C43, C44, C45, C46, C47, C48, C49, C50, C51, C52, C53, C54, C55, C56, C57, C58, C59, C60, C61, C62, C63, C64, C65, C67: 100n; C_0603_1608Metric; JLC 0603
D7, D8, D9, D10, D11, D12, D13, D14, D17, D18, D19, D20, D22, D23, D24, D25, D26, D27, D28, D29, D30, D31, D32, D33, D34, D35, D36, D37, D38, D39, D40, D41, D42, D43, D44, D45, D46, D47, D48, D49, D50, D51, D52, D53, D55: WS2812B-2020; LED_WS2812B-2020_PLCC4_2.0x2.0mm; JLC SMS,2x2mm
JP1: Jumper_2_Bridged; R_0402_1005Metric; JLC 0402

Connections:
/RL_START: D25.3 (DIN); also elsewhere on the board
/rear_light_leds/MID: D42.3 (DIN), D52.1 (DOUT); also elsewhere on the board
GND: C21.2, C23.2, C24.2, C25.2, C26.2, C27.2, C28.2, C29.2, C30.2, C31.2, C32.2, C33.2, C34.2, C35.2, C36.2, C37.2, C38.2, C39.2, C40.2, C41.2, C42.2, C43.2, C44.2, C45.2, C46.2, C47.2, C48.2, C49.2, C50.2, C51.2, C52.2, C53.2, C54.2, C55.2, C56.2, C57.2, C58.2, C59.2, C60.2, C61.2, C62.2, C63.2, C64.2, C65.2, C67.2, D7.2 (VSS), D8.2 (VSS), D9.2 (VSS), D10.2 (VSS), D11.2 (VSS), D12.2 (VSS), D13.2 (VSS), D14.2 (VSS), D17.2 (VSS), D18.2 (VSS), D19.2 (VSS), D20.2 (VSS), D22.2 (VSS), D23.2 (VSS), D24.2 (VSS), D25.2 (VSS), D26.2 (VSS), D27.2 (VSS), D28.2 (VSS), D29.2 (VSS), D30.2 (VSS), D31.2 (VSS), D32.2 (VSS), D33.2 (VSS), D34.2 (VSS), D35.2 (VSS), D36.2 (VSS), D37.2 (VSS), D38.2 (VSS), D39.2 (VSS), D40.2 (VSS), D41.2 (VSS), D42.2 (VSS), D43.2 (VSS), D44.2 (VSS), D45.2 (VSS), D46.2 (VSS), D47.2 (VSS), D48.2 (VSS), D49.2 (VSS), D50.2 (VSS), D51.2 (VSS), D52.2 (VSS), D53.2 (VSS), D55.2 (VSS); also elsewhere on the board
unnamed: D8.1 (DOUT), D9.3 (DIN)
unnamed: D10.3 (DIN), D17.1 (DOUT)
unnamed: D10.1 (DOUT), D14.3 (DIN)
unnamed: D7.1 (DOUT), D11.3 (DIN)
unnamed: D11.1 (DOUT), D18.3 (DIN)
unnamed: D12.3 (DIN), D19.1 (DOUT)
unnamed: D12.1 (DOUT), D26.3 (DIN)
unnamed: D9.1 (DOUT), D13.3 (DIN)
unnamed: D13.1 (DOUT), D27.3 (DIN)
unnamed: D14.1 (DOUT), D23.3 (DIN)
unnamed: D17.3 (DIN), D24.1 (DOUT)
unnamed: D18.1 (DOUT), D30.3 (DIN)
unnamed: D19.3 (DIN), D25.1 (DOUT)
unnamed: D20.3 (DIN), D31.1 (DOUT)
unnamed: D8.3 (DIN), D20.1 (DOUT)
unnamed: D22.3 (DIN), D28.1 (DOUT)
unnamed: D22.1 (DOUT), D32.3 (DIN)
unnamed: D23.1 (DOUT), D28.3 (DIN)
unnamed: D24.3 (DIN), D29.1 (DOUT)
unnamed: D7.3 (DIN), D26.1 (DOUT)
unnamed: D27.1 (DOUT), D36.3 (DIN)
unnamed: D29.3 (DIN), D33.1 (DOUT)
unnamed: D30.1 (DOUT), D34.3 (DIN)
unnamed: D31.3 (DIN), D35.1 (DOUT)
unnamed: D32.1 (DOUT), D55.3 (DIN)
unnamed: D33.3 (DIN), D38.1 (DOUT)
unnamed: D34.1 (DOUT), D39.3 (DIN)
unnamed: D35.3 (DIN), D41.1 (DOUT)
unnamed: D36.1 (DOUT), D47.3 (DIN)
unnamed: D37.3 (DIN), D42.1 (DOUT)
unnamed: D37.1 (DOUT), D48.3 (DIN)
unnamed: D38.3 (DIN), D44.1 (DOUT)
unnamed: D39.1 (DOUT), D45.3 (DIN)
unnamed: D40.3 (DIN), D45.1 (DOUT), JP1.1 (A)
unnamed: D40.1 (DOUT), D50.3 (DIN)
unnamed: D41.3 (DIN), D46.1 (DOUT)
unnamed: D43.3 (DIN), D48.1 (DOUT)
unnamed: D43.1 (DOUT), D53.3 (DIN)
unnamed: D44.3 (DIN), D49.1 (DOUT)
unnamed: D46.3 (DIN), D50.1 (DOUT), JP1.2 (B)
unnamed: D47.1 (DOUT), D51.3 (DIN)
unnamed: D49.3 (DIN), D53.1 (DOUT)
unnamed: D51.1 (DOUT), D52.3 (DIN)
VDD: C21.1, C23.1, C24.1, C25.1, C26.1, C27.1, C28.1, C29.1, C30.1, C31.1, C32.1, C33.1, C34.1, C35.1, C36.1, C37.1, C38.1, C39.1, C40.1, C41.1, C42.1, C43.1, C44.1, C45.1, C46.1, C47.1, C48.1, C49.1, C50.1, C51.1, C52.1, C53.1, C54.1, C55.1, C56.1, C57.1, C58.1, C59.1, C60.1, C61.1, C62.1, C63.1, C64.1, C65.1, C67.1, D7.4 (VDD), D8.4 (VDD), D9.4 (VDD), D10.4 (VDD), D11.4 (VDD), D12.4 (VDD), D13.4 (VDD), D14.4 (VDD), D17.4 (VDD), D18.4 (VDD), D19.4 (VDD), D20.4 (VDD), D22.4 (VDD), D23.4 (VDD), D24.4 (VDD), D25.4 (VDD), D26.4 (VDD), D27.4 (VDD), D28.4 (VDD), D29.4 (VDD), D30.4 (VDD), D31.4 (VDD), D32.4 (VDD), D33.4 (VDD), D34.4 (VDD), D35.4 (VDD), D36.4 (VDD), D37.4 (VDD), D38.4 (VDD), D39.4 (VDD), D40.4 (VDD), D41.4 (VDD), D42.4 (VDD), D43.4 (VDD), D44.4 (VDD), D45.4 (VDD), D46.4 (VDD), D47.4 (VDD), D48.4 (VDD), D49.4 (VDD), D50.4 (VDD), D51.4 (VDD), D52.4 (VDD), D53.4 (VDD), D55.4 (VDD); also elsewhere on the board

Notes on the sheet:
components on this sheet are only populated when using as light JP1 has to be populated, when using as 16 LED taillight

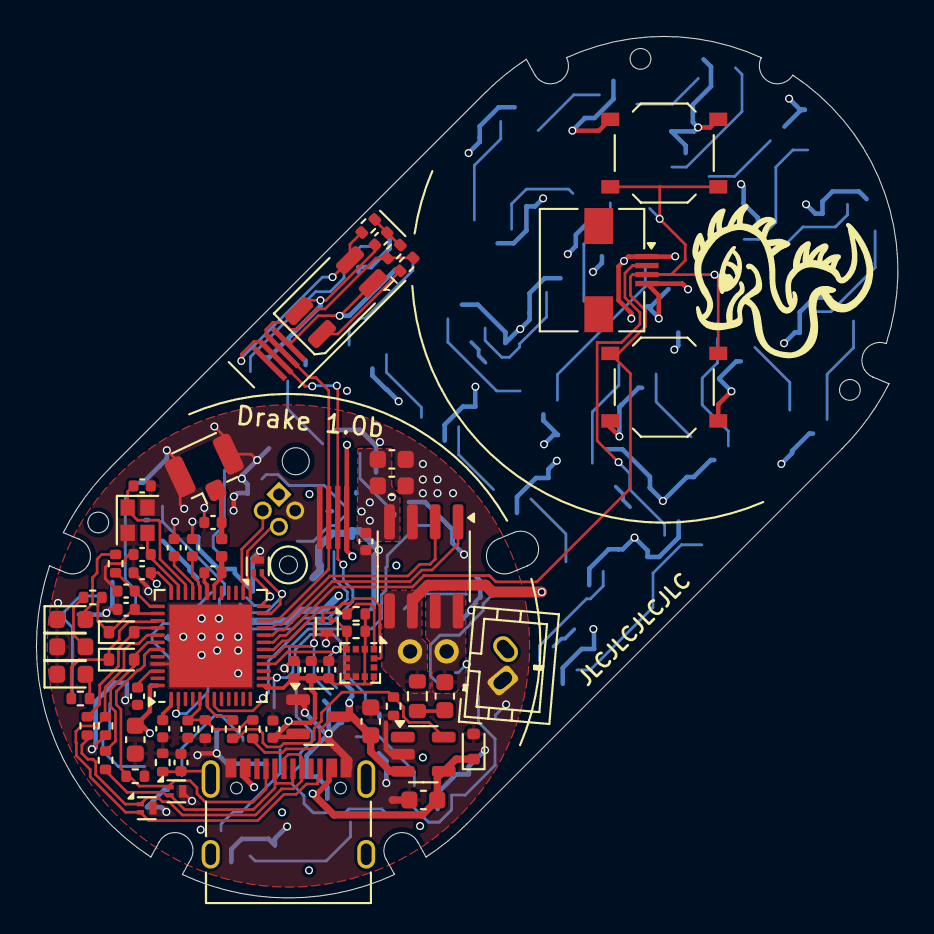
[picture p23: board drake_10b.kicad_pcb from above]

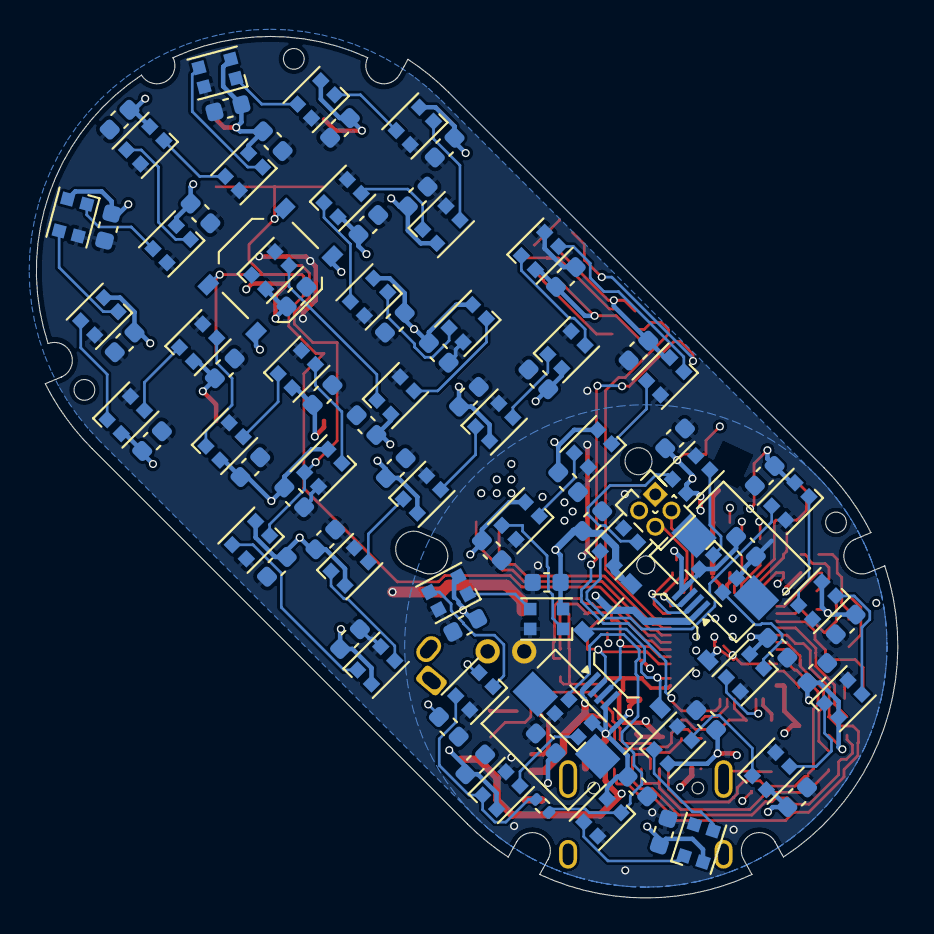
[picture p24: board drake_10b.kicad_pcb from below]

Board: 4 copper layers, 47.9 x 47.9 mm, 167 parts (96 on the bottom side), 91 nets.

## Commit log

2025-06-22 added step file
    [Drake_Fox_2208_v2-case.step, Drake_Fox_2208_v2-plunger.step]
2025-07-02 modified thread and gearbox
    [Drake_Fox_2208_v2-case.step, Drake_Fox_2208_v2-plunger.step, Drake_Fox_2208_v2-plunger.stl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]
2025-07-02 revised production files
    [bom.csv, drake_10b.csv, drake_10b.kicad_pcb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]
